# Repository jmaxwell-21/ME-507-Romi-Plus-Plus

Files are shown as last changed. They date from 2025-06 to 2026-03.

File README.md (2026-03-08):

# ME 507 Romi++ Project

Design repository for Romi++, a self-balancing differential drive robot developed for Cal Poly's ME 507 Mechanical Control Systems Design class.

## Documentation

[View the complete Doxygen code documentation](https://jmaxwell-21.github.io/ME-507-Romi-Plus-Plus/)

## GitHub File Structure

- `Firmware/` - STM32CubeIDE project source code and FSM diagrams
- `Hardware/` - Mechanical and electrical design files and information
- `Media/` -  Project photos and videos
- `docs/` - Doxygen-generated HTML documentation

---

Made by Jack Maxwell  
Cal Poly | Spring 2025

# Overview

Romi++ is a two-wheeled differential drive robot with a cylindrical body. It can be remotely controlled by either a computer or the custom [Smart Knob Controller](https://github.com/Larson-Nick/SmartKnobController) built by my partner and can drive at speeds up to 1&nbsp;m/s while autonomously maintaining balance through PID control.

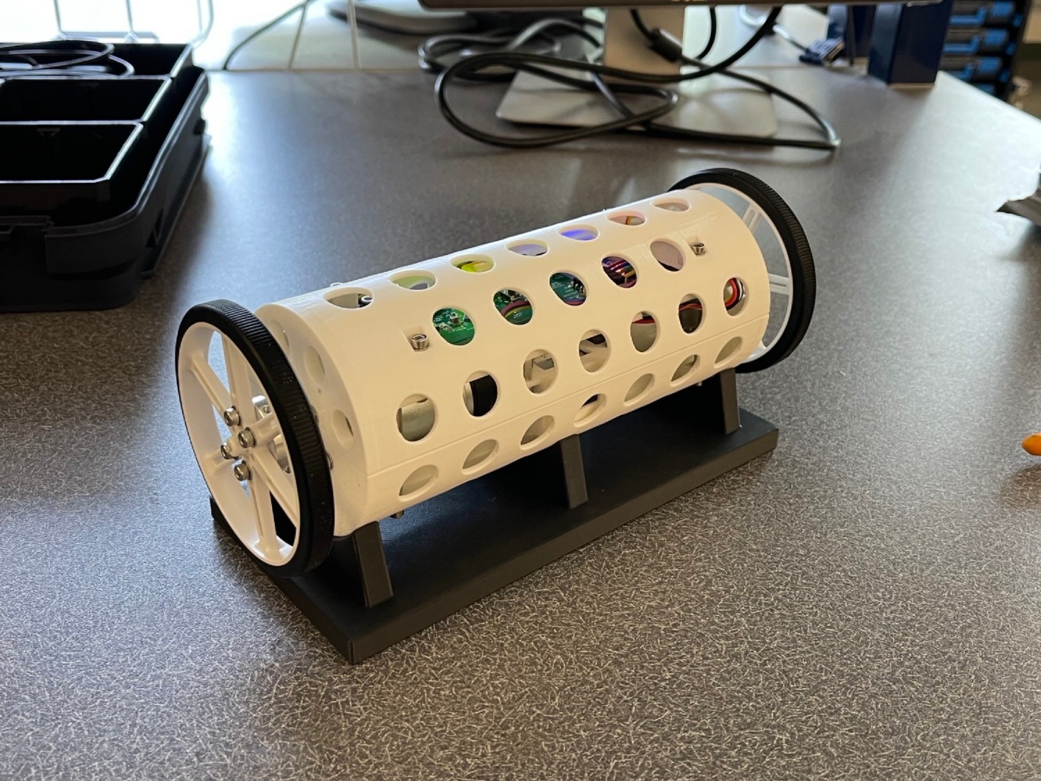
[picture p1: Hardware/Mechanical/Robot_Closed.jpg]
Robot photo


## See Romi++ in action!
<table>
  <tr>
    <td align="center" valign="top">
      <a href="https://youtube.com/shorts/c_1nM_AD648">
        <br>
        <strong>Official Project Demo</strong>
      </a>
      <p>Official project demo showcasing wireless two-wheeled robot with custom controller (using attachments before balance control was implemented).</p>
    </td>
    <td align="center" valign="top">
      <a href="https://youtube.com/shorts/LBDbpKdLq8A">
        <br>
        <strong>Bonus Project Demo</strong>
      </a>
      <p>Final demo with balance control enabled, allowing the robot to stay level while driving without attachments.</p>
    </td>
  </tr>
</table>

This project serves as a successor to my [Romi Line-Following Robot](https://github.com/finite-colin-machine/ME-405-Romi) project from ME 405 at Cal Poly. Unlike the original Romi, which used caster wheels for stability, Romi++ is cylindrical and free to rotate about its drive axis, requiring active balance control to remain upright.

Romi++ was my term project for the ME 507 Mechanical Control Systems Design class at Cal Poly. It was a perfect blend of the four core areas of mechatronics: mechanical design, electronics, embedded systems, and control systems. These aspects of my project are explained in more depth below.

## Mechanical Design

Mechanical Design

The main components of the robot are the 3D-printed cylindrical body, two motors with wheels, a battery compartment, and various fasteners. The motors are mounted beneath the mounting plate and screw into the cylinder sides. The battery sits in a small box beneath the mounting plate, while the electronics rest on top. Long standoffs connect both cylinder halves to the mounting plate.

All 3D-printed components were custom designed, while purchased components (motors, wheels, battery, fasteners) were integrated into the assembly. The challenge was ensuring proper fitment and mounting points for each component. I imported vendor-supplied CAD models into SolidWorks and iteratively refined the design to accommodate all components with appropriate mounting holes and clearances.

See the [Mechanical Design](Hardware/Mechanical) folder for more information on specific components.

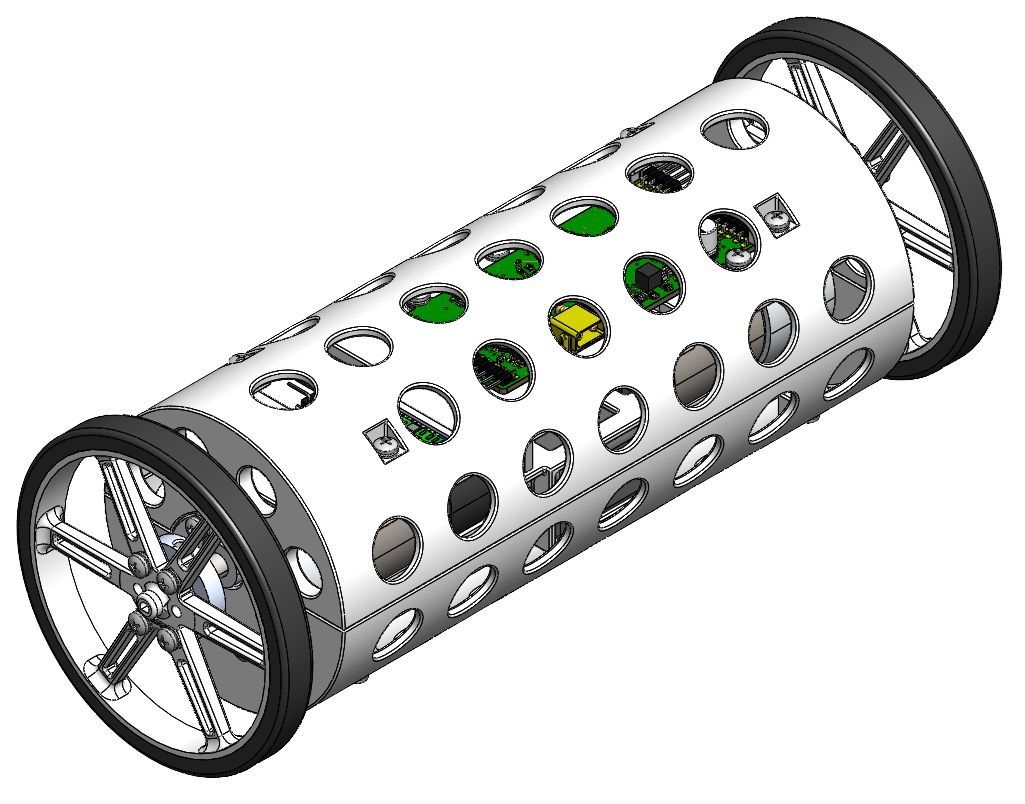
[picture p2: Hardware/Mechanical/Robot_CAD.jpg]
Robot CAD


## Electrical Design

PCB

The PCB that I designed for Romi++ was my first experience with electronics design. It took up a significant portion of the 10-week course, but it was worth it for all of the experience I gained (and the fun I had)!

The PCB has 9 main components: the power distribution system to supply various voltage levels to the system, the STM32 microcontroller to control all the components, an IMU to measure heading and pitch, 2 drivers and pin headers for the motors, a pin header for the HC-05 Bluetooth module, a pin header for the ST-Link debugger, a reset button, and a general-purpose user button. I designed the [schematic](Hardware/Electrical/PCB%20Schematic.pdf) and board layout in Fusion 360 and had it manufactured by JLCPCB.

See the [Electrical Design](Hardware/Electrical) folder for complete schematics, board layouts, and manufacturing files.

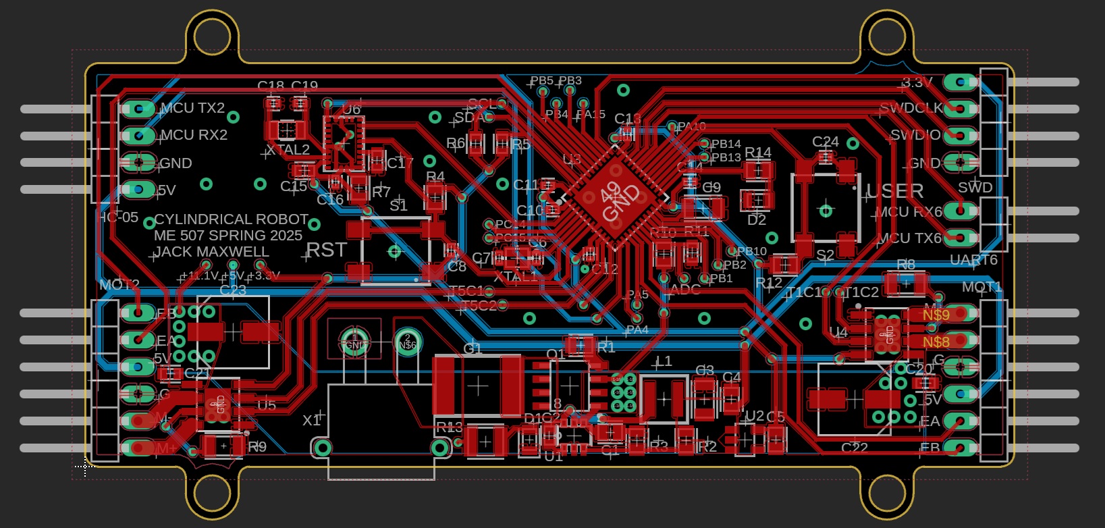
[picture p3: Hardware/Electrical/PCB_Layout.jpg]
Board Layout


### Power Distribution

The robot is powered by a 3S LiPo battery with a nominal voltage of 11.1&nbsp;V. A [fuse](https://www.digikey.com/en/products/detail/littelfuse-inc/2920l400-15mr/6234817) and a [p-channel MOSFET](https://www.digikey.com/en/products/detail/infineon-technologies/IRF7416TRPBF/856470) are used for circuit protection, and the 11.1&nbsp;V from the battery goes to the two [motor driver](https://www.digikey.com/en/products/detail/texas-instruments/DRV8231DDAR/16184249) integrated circuits. A [buck regulator](https://www.digikey.com/en/products/detail/texas-instruments/lmr54406fdbvr/15926505) is used to drop the 11.1&nbsp;V to 5&nbsp;V and provide a smooth output for the encoders and the [HC-05](https://www.electronicwings.com/sensors-modules/bluetooth-module-hc-05-), and an [LDO regulator](https://www.digikey.com/en/products/detail/texas-instruments/TPS7A2033PDBVR/13566866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) is used to drop the 5&nbsp;V to 3.3&nbsp;V to power the remaining integrated circuits.

### Microcontroller (MCU)

To run my code and control each peripheral, an [STM32F411CEU6 Microcontroller](https://www.digikey.com/en/products/detail/stmicroelectronics/STM32F411CEU6/4935720) is used. This 32-bit ARM Cortex-M4 MCU running at 100&nbsp;MHz provides sufficient processing power for real-time control loops while offering the necessary peripherals: I2C for the IMU, UART for Bluetooth communication, PWM timers for motor control, and encoder inputs for wheel speed measurement.

### Inertial Measurement Unit (IMU)

To provide heading (yaw) and pitch measurements for the robot's control system, the [BNO055](https://www.digikey.com/en/products/detail/bosch-sensortec/BNO055/6136301) 9-axis absolute orientation sensor is used. The heading data enables precise turning control, while the pitch angle is used by the balance controller to keep the robot upright. Communication with the microcontroller occurs over I2C, with the sensor providing orientation data at up to 100&nbsp;Hz for responsive control.

## Firmware and Controls

The firmware for Romi++ was developed in C/C++ using STM32CubeIDE. While driver implementations can be found in the [Firmware](Firmware) folder, this section focuses on the cooperative multitasking structure and Finite State Machine (FSM) control algorithms that enable the robot's movement.

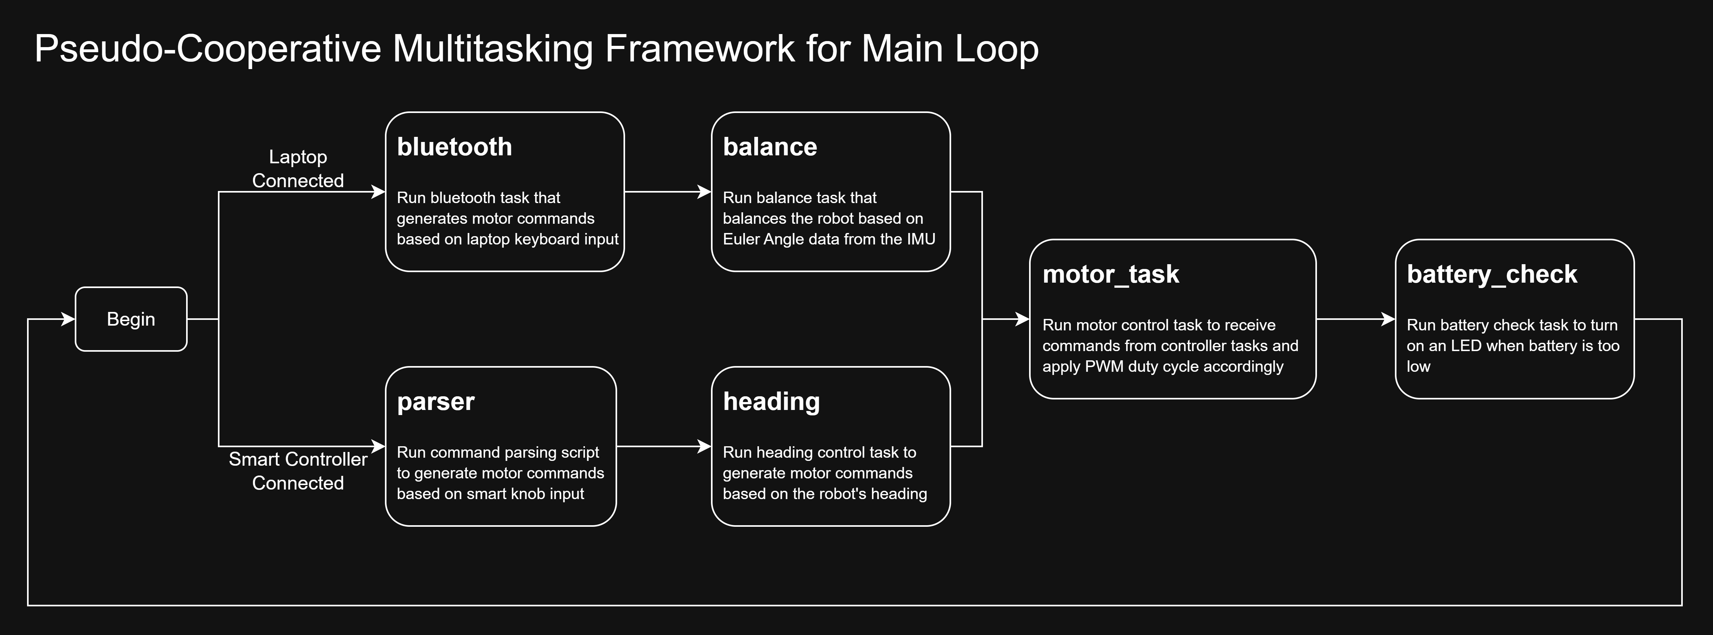
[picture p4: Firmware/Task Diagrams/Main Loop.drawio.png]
Main Loop


The firmware uses a pseudo-cooperative multitasking framework where tasks execute sequentially in the main loop. Based on the connected controller (laptop or Smart Knob), different control tasks run in order, each completing its work before passing control to the next task.

### Bluetooth Task

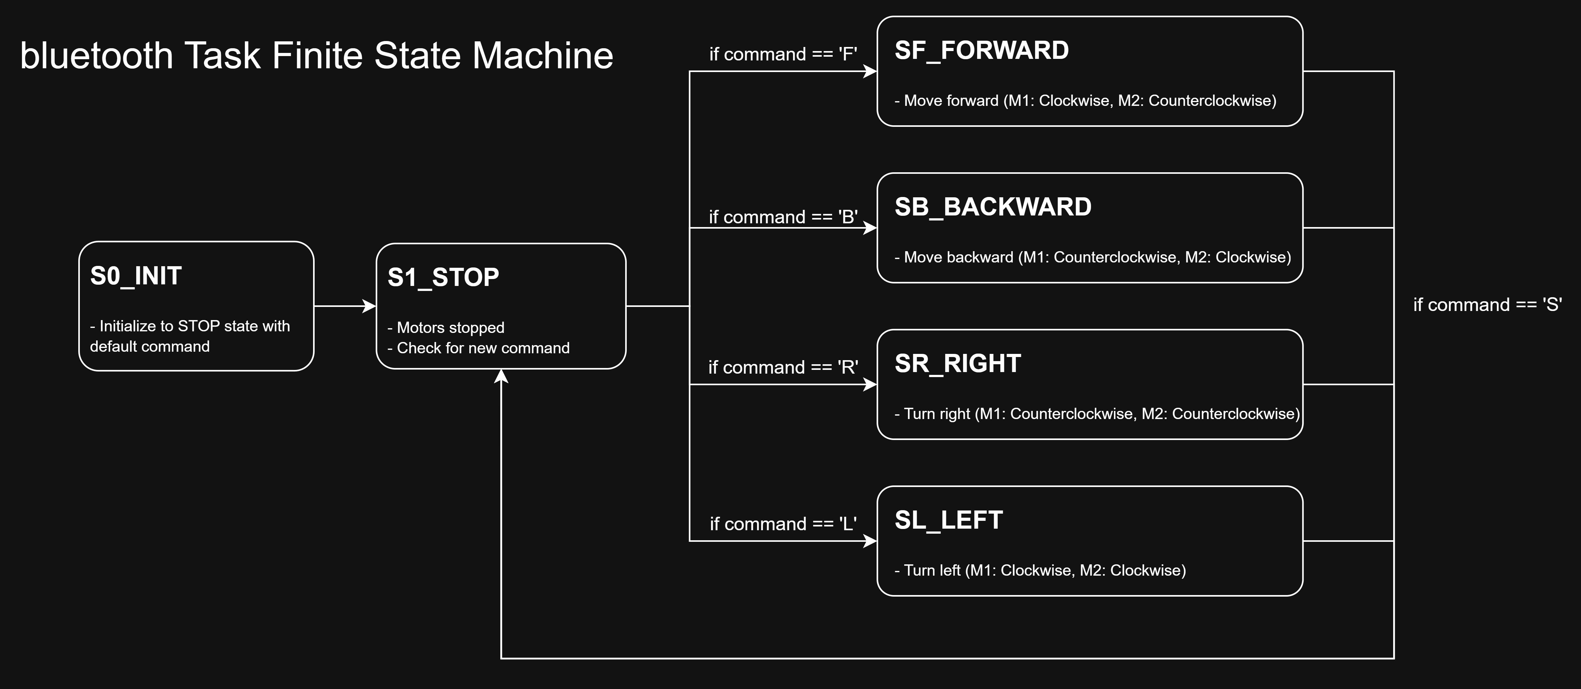
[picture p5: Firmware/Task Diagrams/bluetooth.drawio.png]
bluetooth


When a laptop is connected, the Bluetooth task runs and decodes signals sent by the [robot controller](Firmware/Additional%20Code/Robot%20Controller.py) Python script. Based on which key is pressed, the task transitions between states that command the motors to move forward, backward, left, or right. When no keys are pressed, it returns to the STOP state. This control interface was primarily used for solo testing, while the custom controller served as the main input method.

### Balance Task

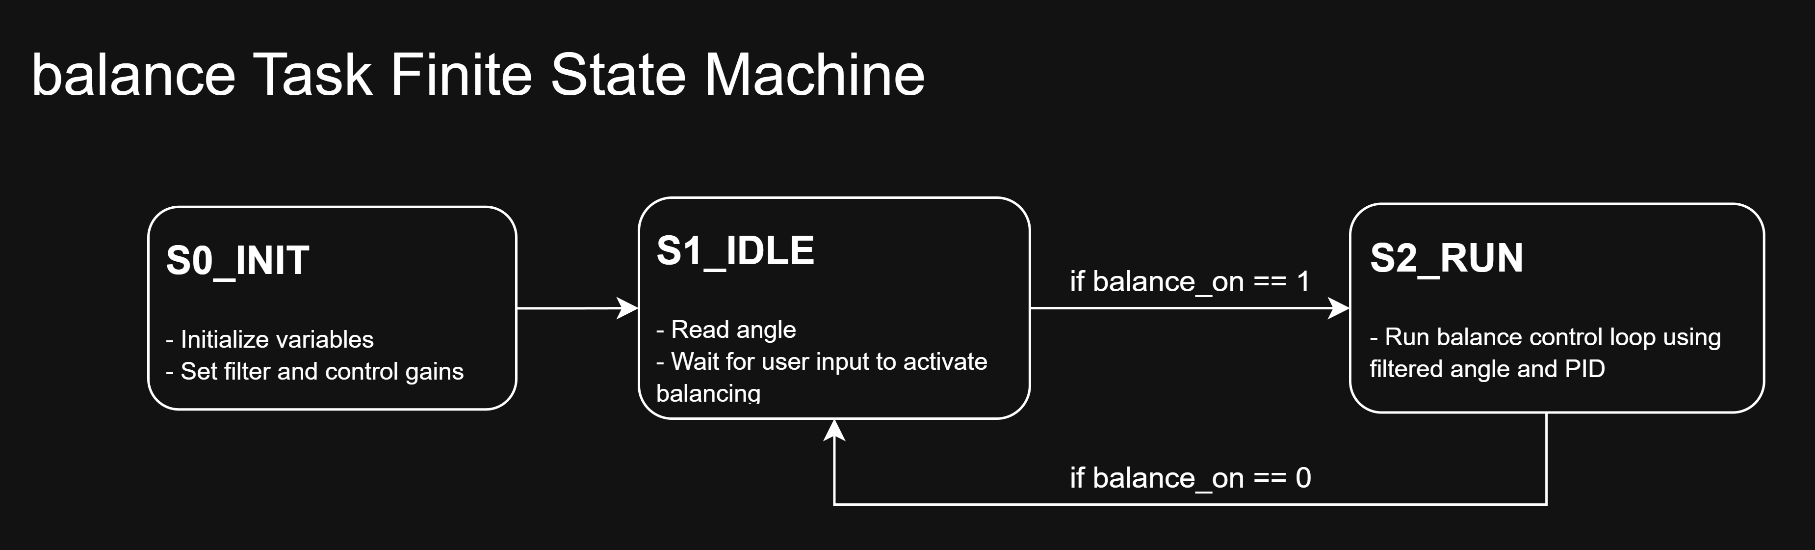
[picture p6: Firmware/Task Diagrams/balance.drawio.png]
balance


When a laptop is connected, the Balance task reads the pitch angle from the IMU and applies balance control to keep the robot upright. Because the robot is free to rotate about its drive axis, the cylindrical body tilts when the motors spin in the same direction. Without active balance control, the robot cannot drive effectively.

A PID controller compares the current pitch angle to the setpoint (0 degrees) and outputs a corrective motor effort that gets sent to the motor task. This creates a feedback loop that continuously adjusts the motors to maintain balance while driving.

The balance control toggles between IDLE and RUN states when the user button on the PCB is pressed. This allows demonstration of the robot's behavior with and without balance control enabled.

Balance control was not implemented in time for the official project demonstration, which is why an attachment was used to prevent the robot from spinning in that demo. This is also why balance control only runs while a laptop is connected and not with the Smart Knob Controller.

### Parser Task

The Parser task decodes command strings received from the Smart Knob Controller via UART IDLE-line detection with DMA reception. Commands begin with a mode character ('A', 'B', 'C', or 'D') followed by hexadecimal values for motor duty cycles or heading setpoints. The parser extracts these values and makes them available to the motor and heading control tasks.

**Supported modes:**
- **Mode A/B**: Direct motor control (M1 and M2 duty cycles)
- **Mode C**: Reserved for future use
- **Mode D**: Combined heading and motor effort control

### Heading Task

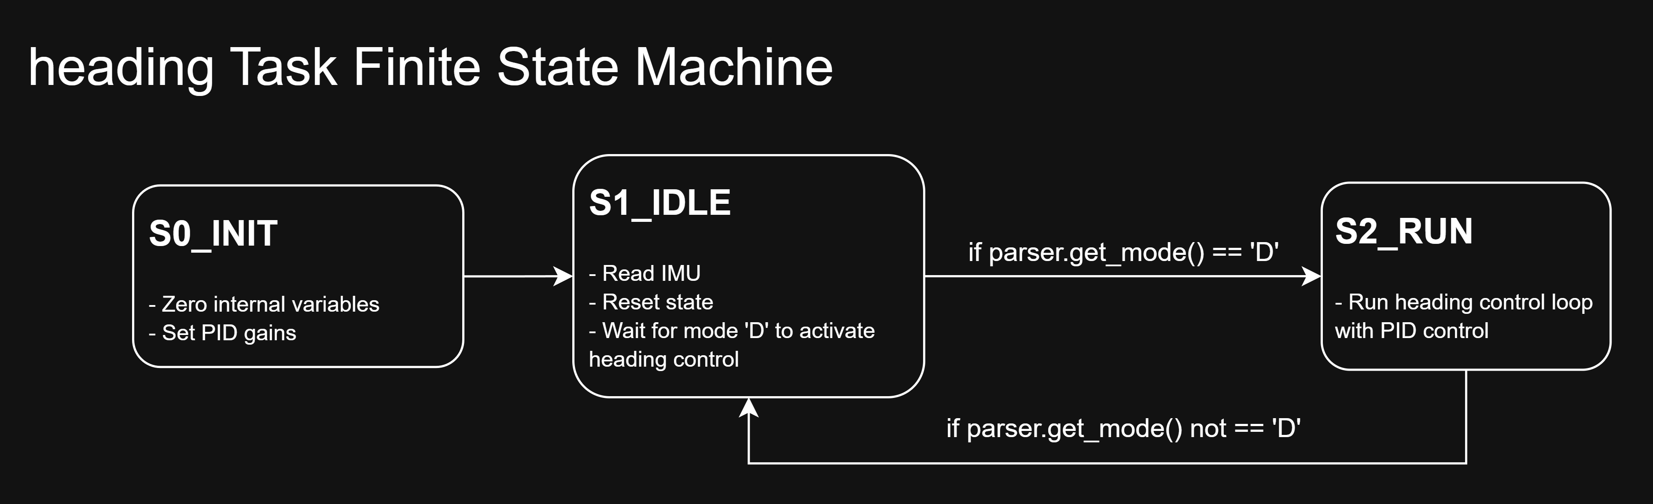
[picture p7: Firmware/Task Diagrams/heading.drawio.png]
heading


When Mode D is active (combined heading and motor control from the Smart Knob Controller), the Heading task reads the yaw angle from the IMU and controls the robot's orientation. The task tracks the robot's angular position by accumulating angle changes while handling 360-degree wraparound, creating a continuous heading reference.

A PID controller compares the current heading to the commanded setpoint and generates opposing motor efforts for differential steering. These efforts are added to any forward/backward motion commands, allowing the robot to drive while maintaining orientation.

The heading control activates only in Mode D and returns to IDLE when the controller switches modes. Pressing the user button calibrates the heading by resetting the accumulated position to match the current setpoint, which is useful for correcting drift or realigning the reference frame during operation.

### Motor Task

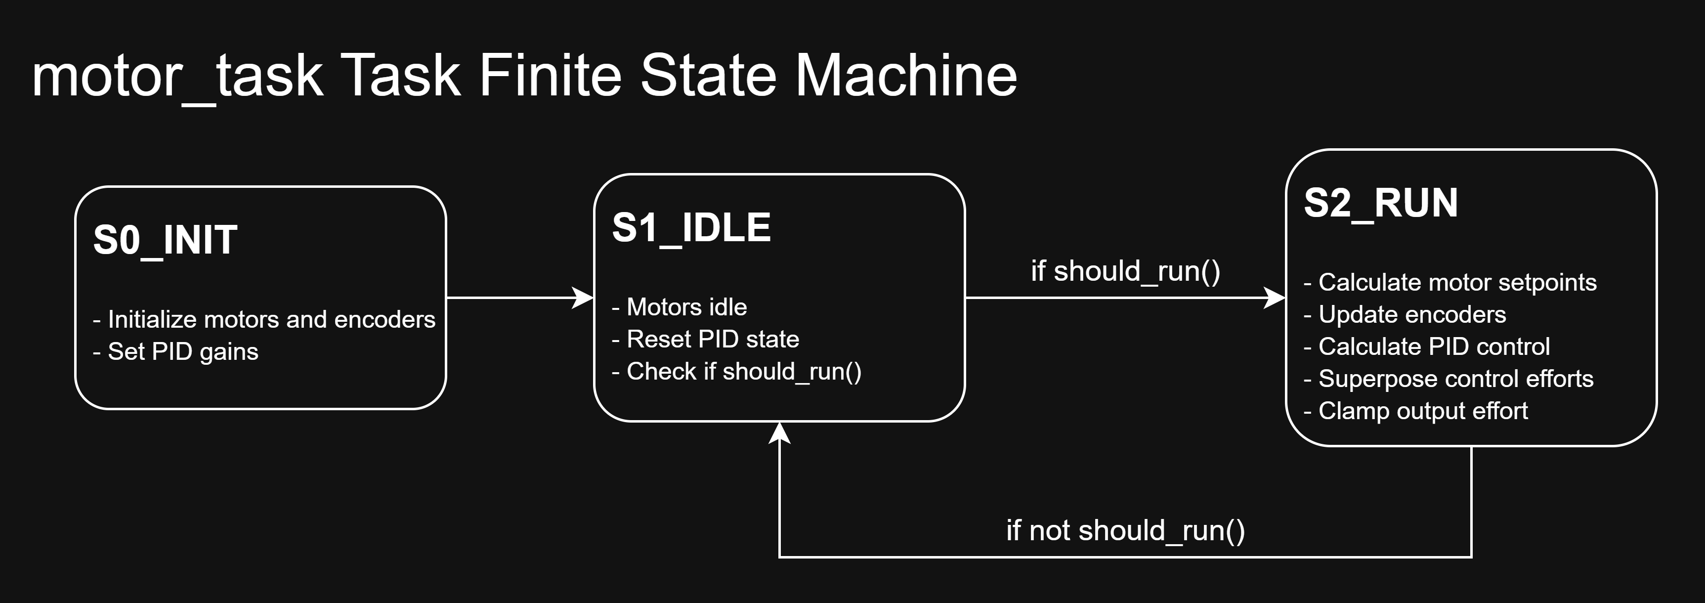
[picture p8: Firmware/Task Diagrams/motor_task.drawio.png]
motor_task


The Motor task serves as the central control hub that integrates commands from all other tasks and translates them into PWM signals for the motor drivers. It receives speed setpoints from either the Bluetooth or Parser tasks and uses encoder feedback to implement closed-loop speed control with PID.

The task continuously reads encoder speeds and calculates PID corrections to match the commanded wheel velocities. Crucially, it then superposes control efforts from the Heading and Balance tasks onto these base speed commands. This allows the robot to simultaneously drive at a target speed, maintain orientation, and stay upright.

The motor task transitions from IDLE to RUN whenever any input source provides non-zero commands or control efforts. Final motor efforts are clamped to safe PWM limits before being sent to the motor drivers, ensuring the robot operates within hardware constraints. This architecture makes the Motor task the final stage in a layered control system where multiple independent controllers work together to achieve complex behavior.

### Battery Check Task

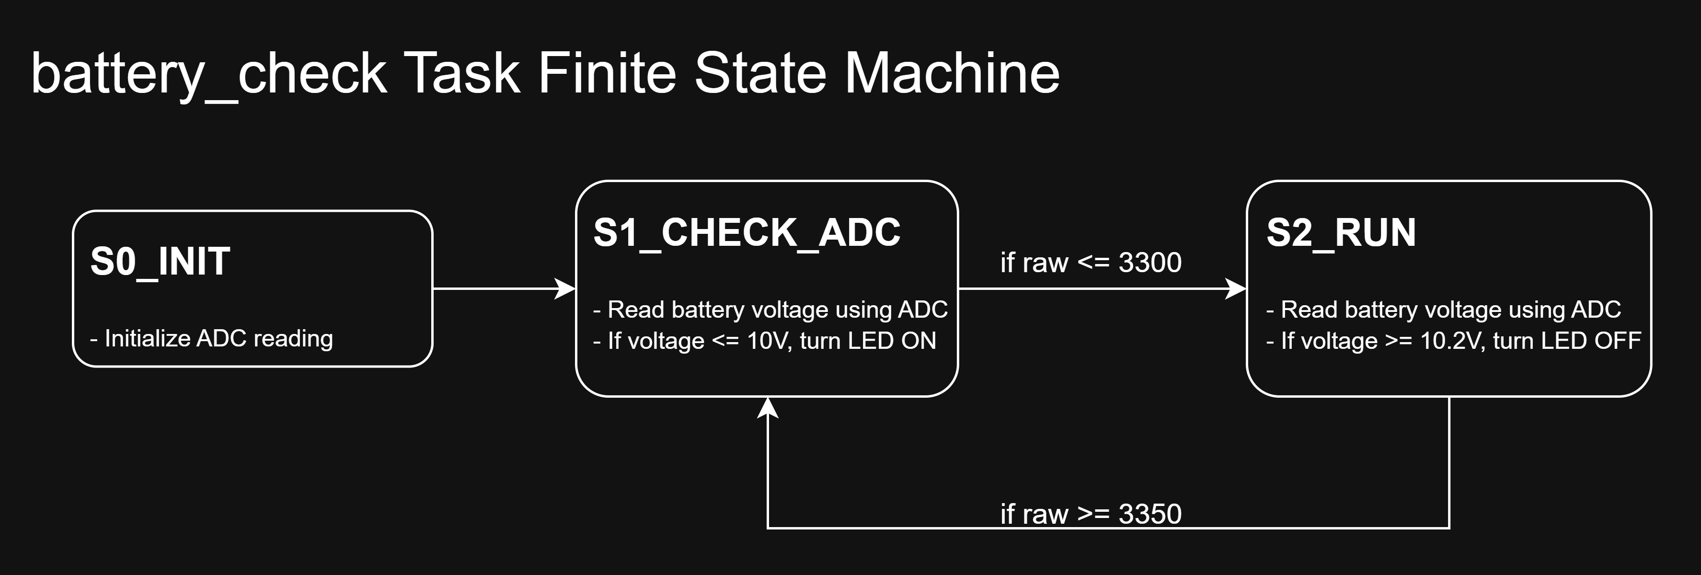
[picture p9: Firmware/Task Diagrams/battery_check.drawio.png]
battery_check


The Battery Check task monitors the battery voltage through an ADC input and provides a visual warning when power drops too low. It continuously reads the analog voltage level and compares it against threshold values to protect the LiPo battery from over-discharge.

When the battery voltage drops below approximately 10.05 V (ADC value < 3300), the task activates an LED indicator and transitions to the BATTERY_LOW state. Once in this state, the LED remains on until the voltage recovers to at least 10.20 V (ADC value > 3350), at which point it turns off and returns to normal monitoring.

This design prevents the LED from flickering on and off when the battery voltage hovers near the threshold, as motor loads can cause temporary voltage dips that recover quickly. When the battery is depleted and requires charging, it must be disconnected to do so. The specific voltage thresholds are chosen to provide a safe margin above the 3 V per cell over-discharge limit (9 V total for a 3S battery).

## Project Results and Reflection

Romi++ successfully demonstrates the integration of mechanical design, electronics, embedded systems, and control systems into a fully functional balancing robot. The final system achieves autonomous balance control, precise heading tracking, and wireless operation through two independent control interfaces.

**Key achievements:**
- DFMA-driven design with standardized fasteners and single-tool access
- Custom PCB design and fabrication with successful implementation
- Multi-layered control architecture with superposed PID controllers
- Wireless control via Bluetooth for laptop and custom controller interfaces

**Challenges and lessons learned:**

Designing the PCB was a grueling task, especially with no prior experience. Over about 4 weeks, I learned about decoupling capacitors, ground planes, trace routing, and many more topics while iterating and improving my design. The end result was a board with no defects that worked perfectly on the first try, which is something I am very proud of!

With only 3 weeks to write and test the code after receiving the PCB, the project required careful prioritization of features. Before implementing balance control, I first had to ensure my robot could communicate with the Smart Knob Controller and interpret its commands for the project demo. Tuning multiple PID controllers required systematic testing documented in the [project videos](Media).

**Future improvements:**
- Enable Bluetooth connection with Xbox/PlayStation controller for more versatile and intuitive control
- Optimize PID gains for faster response and better disturbance rejection
- Create a new iteration with omnidirectional movement, jumping capabilities, and a built-in camera, similar to the [drones in Rainbow Six Siege](https://rainbowsix.fandom.com/wiki/Drone)

This project provided hands-on experience across the full mechatronics design cycle, from initial CAD modeling through PCB design to firmware development and control system tuning. Special thanks to [Nick Larson](https://github.com/Larson-Nick) for developing the Smart Knob Controller that elevated this project's user experience.

## Media Gallery
Check out the [Media folder](Media) for photos and videos of project development. Watch the [full video playlist](https://www.youtube.com/playlist?list=PLDFOiaVsUKKqYprYMNDaC-OZPWteVwOPU) to see the robot's development from first tests to final demonstration.

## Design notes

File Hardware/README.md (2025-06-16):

# Hardware

This folder contains all electrical and mechanical design files for the Romi++ Differential Drive Robot, including PCB schematics, board layout, manufacturing assets, and CAD models.

## Contents

### `Electrical/` – Fusion PCB design files, manufacturing exports, and board reference images

- `JLCPCB Order Info/` – Gerber files, bill of materials (BOM), and pick-and-place data for PCB fabrication, see notes for more info
- `PCB Design Files/` – Schematic (`.sch`), board layout (`.brd`), 3D model (`.step`), and full Fusion 360 project archive (`.f3z`)
- Additional Files – Reference images of the board, schematic and layout PDFs

### `Mechanical/` – SolidWorks CAD files, 3D-printable models, and robot images

- `SolidWorks 2024 Part Files/` – Native `.SLDPRT` and `.SLDASM` files, including McMaster-Carr fasteners and vendor-supplied STEP models
- `STL 3-D Print Files/` – Exported `.stl` files ready for 3D printing
- `Robot BOM.csv` - Bill of materials for the mechanical assembly, see notes for more info
- Additional Files – Images of the assembled robot and CAD assembly

---

## How to Open the Files

### SolidWorks Files

1. Launch **SolidWorks 2024** or compatible version
2. Open `.SLDASM` files from `SolidWorks 2024 Part Files/`
3. Make sure subfolders (e.g., fasteners, STEP parts) are in the same root for proper assembly resolution

### Fusion 360 Files

1. Open Fusion 360
2. Go to **File → Open**
3. Select `ME 507 Romi++.f3z` to import the PCB project including schematic and layout

---

## Notes

- Mechanical Notes
    - Components not included in BOM were provided by my instructor
    - 20  8mm M3 Screws
    - 12 10mm M3 Screws
    - 12 12mm M3 Screws
    - 44 M3 Washers (.5mm thick)
    -  8 M3 Hex Nuts
- Electrical notes
    - For the JLCPCB order, some PCB components needed to be adjusted. This consisted of rotating some parts into the correct orientation seen on my board layout. For any recreations of this project, it is highly recommended to have the manufacturer review the design for you before assembly begins.

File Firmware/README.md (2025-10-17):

# Firmware

This folder contains the full STM32CubeIDE project for the STM32F411 microcontroller used in the Romi++ Differential Drive Robot.

## Contents

- `Core/` – Source code and header files for all robot software
- `Drivers/` – HAL drivers for peripherals
- `.ioc` file – STM32CubeMX configuration file
- `.project` and `.cproject` – Eclipse project files for STM32CubeIDE

- `Additional Code/` - Python script for controlling robot and STM32CubeIDE project for HC-05 Bluetooth Module configuration
- `Task Diagrams/` - Task diagrams for each FSM shown on the main page

## How to Open the Project

To open this project in STM32CubeIDE:

### Option 1: Import via `.ioc` File

1. Open STM32CubeIDE
2. Go to **File → Open Projects from File System**
3. Click **Directory…** and select the `firmware/` folder
4. STM32CubeIDE will automatically detect and import the project
5. Click **Finish**

### Option 2: Open `.project` Directly

1. Double-click the `.project` file in the `firmware/` folder
2. STM32CubeIDE will open it as a recognized workspace project

---

## Notes

- The `.ioc` file defines all clock settings, pin mappings, and peripheral configurations
- Any changes made in `.ioc` can regenerate code in `Core/` and `Drivers/`

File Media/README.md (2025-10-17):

# Project Media

This folder contains all photos and videos of my project throughout its development.

## Demonstration Videos
<table>
  <tr>
    <td align="center" valign="top">
      <a href="https://youtube.com/shorts/c_1nM_AD648">
        <br>
        <strong>First Project Demo</strong>
      </a>
      <p>Official project demo showcasing wireless two-wheeled robot with custom controller (using attachments before balance control was implemented).</p>
    </td>
    <td align="center" valign="top">
      <a href="https://youtube.com/shorts/LBDbpKdLq8A">
        <br>
        <strong>Final Project Demo</strong>
      </a>
      <p>Final demo with balance control enabled, allowing the robot to stay level while driving without attachments.</p>
    </td>
  </tr>
</table>

## Testing Videos
<table>
  <tr>
    <td align="center" valign="top">
      <a href="https://youtube.com/shorts/n4RnW4XA5BE">
        <br>
        <strong>First System Test</strong>
      </a>
      <p>Initial PCB test verifying motor control functionality.</p>
    </td>
    <td align="center" valign="top">
      <a href="https://youtube.com/shorts/uIjkk4RzHAo">
        <br>
        <strong>Bluetooth Driving Test 1</strong>
      </a>
      <p>First wireless driving test using Bluetooth control from laptop, with attachments to prevent spinning.</p>
    </td>
    <td align="center" valign="top">
      <a href="https://youtube.com/shorts/yojhLrzBfxM">
        <br>
        <strong>Bluetooth Driving Test 2</strong>
      </a>
      <p>Second Bluetooth driving test with attachments removed, showing free spinning before balance control.</p>
    </td>
    <td align="center" valign="top">
      <a href="https://youtube.com/shorts/kFbRjYCwOs8">
        <br>
        <strong>IMU Display Test</strong>
      </a>
      <p>First IMU test demonstrating real-time heading angle updates.</p>
    </td>
  </tr>
  <tr>
    <td align="center" valign="top">
      <a href="https://youtube.com/shorts/kPtjlTdcE0k">
        <br>
        <strong>Heading Control Test 1</strong>
      </a>
      <p>Initial heading control test with unstable behavior due to poor PID tuning.</p>
    </td>
    <td align="center" valign="top">
      <a href="https://youtube.com/shorts/aGWxtnayLmA">
        <br>
        <strong>Heading Control Test 2</strong>
      </a>
      <p>Improved heading controller that worked at 0 degrees but lacked robustness.</p>
    </td>
    <td align="center" valign="top">
      <a href="https://youtube.com/shorts/tQbPDnsnWS4">
        <br>
        <strong>Heading Control Test 3</strong>
      </a>
      <p>Final heading controller demonstrating quick, accurate response with minimal overshoot.</p>
    </td>
    <td align="center" valign="top">
      <a href="https://youtube.com/shorts/Og49P6c5zbM">
        <br>
        <strong>Controller Integration Test</strong>
      </a>
      <p>First test connecting to lab partner's custom controller for remote operation.</p>
    </td>
  </tr>
  <tr>
    <td align="center" valign="top">
      <a href="https://youtube.com/shorts/0uNJvMxnFvQ">
        <br>
        <strong>Speed Test</strong>
      </a>
      <p>Forward and backward motion test with custom controller at 50% speed.</p>
    </td>
    <td align="center" valign="top">
      <a href="https://youtube.com/shorts/kXgYKft2zP0">
        <br>
        <strong>Balance Control Test 1</strong>
      </a>
      <p>First balance control test using PID on pitch angle with no speed limiter.</p>
    </td>
    <td align="center" valign="top">
      <a href="https://youtube.com/shorts/U_N1_kcBDy4">
        <br>
        <strong>Balance Control Test 2</strong>
      </a>
      <p>Second balance control test with 50% speed limit for easier handling.</p>
    </td>
  </tr>
</table>

## Full Playlist
Watch all project videos here: [Project Playlist](https://www.youtube.com/playlist?list=PLDFOiaVsUKKqYprYMNDaC-OZPWteVwOPU)

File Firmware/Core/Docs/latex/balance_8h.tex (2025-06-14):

\doxysection{Inc/balance.h File Reference}
\hypertarget{balance_8h}{}\label{balance_8h}\index{Inc/balance.h@{Inc/balance.h}}

Declaration of the \doxylink{class_b_a_l_a_n_c_e}{BALANCE} class for managing robot balance using a FSM.  

{\ttfamily \#include "{}BNO055\+\_\+\+STM32.\+h"{}}\newline
{\ttfamily \#include "{}time\+\_\+utils.\+h"{}}\newline
{\ttfamily \#include $<$stdint.\+h$>$}\newline
{\ttfamily \#include $<$algorithm$>$}\newline
\doxysubsubsection*{Classes}
\begin{DoxyCompactItemize}
\item 
class \mbox{\hyperlink{class_b_a_l_a_n_c_e}{BALANCE}}
\begin{DoxyCompactList}\small\item\em Finite State Machine class for robot balance control. \end{DoxyCompactList}\end{DoxyCompactItemize}
\doxysubsubsection*{Variables}
\begin{DoxyCompactItemize}
\item 
\Hypertarget{balance_8h_a7871395ef24115844178e306695a6b39}\label{balance_8h_a7871395ef24115844178e306695a6b39} 
\mbox{\hyperlink{struct_b_n_o055___sensors__t}{BNO055\+\_\+\+Sensors\+\_\+t}} {\bfseries BNO055}
\begin{DoxyCompactList}\small\item\em External reference to BNO055 sensor data structure. \end{DoxyCompactList}\item 
\Hypertarget{balance_8h_a59cc8776b62c3d309d2ceafcfbfa504c}\label{balance_8h_a59cc8776b62c3d309d2ceafcfbfa504c} 
volatile bool {\bfseries USER}
\begin{DoxyCompactList}\small\item\em External flag indicating user button press. \end{DoxyCompactList}\end{DoxyCompactItemize}

\doxysubsection{Detailed Description}
Declaration of the \doxylink{class_b_a_l_a_n_c_e}{BALANCE} class for managing robot balance using a FSM. 

This header defines a finite state machine (FSM) class for maintaining balance of a differential drive robot using BNO055 IMU data. It includes PID control logic and internal state tracking.

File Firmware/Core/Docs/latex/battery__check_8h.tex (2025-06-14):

\doxysection{Inc/battery\+\_\+check.h File Reference}
\hypertarget{battery__check_8h}{}\label{battery__check_8h}\index{Inc/battery\_check.h@{Inc/battery\_check.h}}

Header for the \doxylink{class_b_a_t_t_e_r_y___c_h_e_c_k}{BATTERY\+\_\+\+CHECK} class that monitors battery voltage of a 3S Li\+Po battery using the ADC.  

{\ttfamily \#include $<$stm32f4xx\+\_\+hal.\+h$>$}\newline
{\ttfamily \#include $<$stdint.\+h$>$}\newline
\doxysubsubsection*{Classes}
\begin{DoxyCompactItemize}
\item 
class \mbox{\hyperlink{class_b_a_t_t_e_r_y___c_h_e_c_k}{BATTERY\+\_\+\+CHECK}}
\begin{DoxyCompactList}\small\item\em A finite state machine for monitoring battery voltage. \end{DoxyCompactList}\end{DoxyCompactItemize}
\doxysubsubsection*{Variables}
\begin{DoxyCompactItemize}
\item 
\Hypertarget{battery__check_8h_a22b804736f5648d52f639b2647d4ed13}\label{battery__check_8h_a22b804736f5648d52f639b2647d4ed13} 
ADC\+\_\+\+Handle\+Type\+Def {\bfseries hadc1}
\begin{DoxyCompactList}\small\item\em External reference to the ADC handle used for battery sensing. \end{DoxyCompactList}\end{DoxyCompactItemize}

\doxysubsection{Detailed Description}
Header for the \doxylink{class_b_a_t_t_e_r_y___c_h_e_c_k}{BATTERY\+\_\+\+CHECK} class that monitors battery voltage of a 3S Li\+Po battery using the ADC. 

Defines a finite state machine that checks battery level and signals a low voltage condition using GPIO indicators.

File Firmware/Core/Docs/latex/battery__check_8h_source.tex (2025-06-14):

\doxysection{battery\+\_\+check.\+h}
\hypertarget{battery__check_8h_source}{}\label{battery__check_8h_source}\index{Inc/battery\_check.h@{Inc/battery\_check.h}}
\mbox{\hyperlink{battery__check_8h}{Go to the documentation of this file.}}
\begin{DoxyCode}{0}
\DoxyCodeLine{00001\ \textcolor{comment}{/*}}
\DoxyCodeLine{00002\ \textcolor{comment}{\ *\ battery\_check.h}}
\DoxyCodeLine{00003\ \textcolor{comment}{\ *}}
\DoxyCodeLine{00004\ \textcolor{comment}{\ *\ \ Created\ on:\ Jun\ 4,\ 2025}}
\DoxyCodeLine{00005\ \textcolor{comment}{\ *\ \ \ \ \ \ Author:\ jacka}}
\DoxyCodeLine{00006\ \textcolor{comment}{\ */}}
\DoxyCodeLine{00007\ }
\DoxyCodeLine{00008\ \textcolor{preprocessor}{\#ifndef\ INC\_BATTERY\_CHECK\_H\_}}
\DoxyCodeLine{00009\ \textcolor{preprocessor}{\#define\ INC\_BATTERY\_CHECK\_H\_}}
\DoxyCodeLine{00010\ }
\DoxyCodeLine{00017\ }
\DoxyCodeLine{00018\ \textcolor{preprocessor}{\#include\ <stm32f4xx\_hal.h>}}
\DoxyCodeLine{00019\ \textcolor{preprocessor}{\#include\ <stdint.h>}}
\DoxyCodeLine{00020\ }
\DoxyCodeLine{00022\ \textcolor{keyword}{extern}\ ADC\_HandleTypeDef\ \mbox{\hyperlink{battery__check_8h_a22b804736f5648d52f639b2647d4ed13}{hadc1}};}
\DoxyCodeLine{00023\ }
\DoxyCodeLine{00030\ \textcolor{keyword}{class\ }\mbox{\hyperlink{class_b_a_t_t_e_r_y___c_h_e_c_k_aed5ac8125ffc7805a9cf07b1544a488d}{BATTERY\_CHECK}}}
\DoxyCodeLine{00031\ \{}
\DoxyCodeLine{00032\ \textcolor{keyword}{public}:}
\DoxyCodeLine{00037\ \ \ \ \ \textcolor{keyword}{typedef}\ \textcolor{keyword}{enum}\ \mbox{\hyperlink{class_b_a_t_t_e_r_y___c_h_e_c_k_ae999e6f209b67a67364d82a2820553a2}{state}}}
\DoxyCodeLine{00038\ \ \ \ \ \{}
\DoxyCodeLine{00039\ \ \ \ \ \ \ \ \ \mbox{\hyperlink{class_b_a_t_t_e_r_y___c_h_e_c_k_ae999e6f209b67a67364d82a2820553a2a2efb3206dce96a77ef043a7b0598337f}{S0\_INIT}},\ \ \ \ \ \ \ \ \ }
\DoxyCodeLine{00040\ \ \ \ \ \ \ \ \ \mbox{\hyperlink{class_b_a_t_t_e_r_y___c_h_e_c_k_ae999e6f209b67a67364d82a2820553a2ab7b987c14e4c84315b0df446d7552718}{S1\_CHECK\_ADC}},\ \ \ \ }
\DoxyCodeLine{00041\ \ \ \ \ \ \ \ \ \mbox{\hyperlink{class_b_a_t_t_e_r_y___c_h_e_c_k_ae999e6f209b67a67364d82a2820553a2a6fd5d034e05dfe1a3f98d474c8f8a6fc}{S2\_BATTERY\_LOW}}\ \ \ }
\DoxyCodeLine{00042\ \ \ \ \ \}\ state\_t;}
\DoxyCodeLine{00043\ }
\DoxyCodeLine{00047\ \ \ \ \ \mbox{\hyperlink{class_b_a_t_t_e_r_y___c_h_e_c_k_aed5ac8125ffc7805a9cf07b1544a488d}{BATTERY\_CHECK}}();}
\DoxyCodeLine{00048\ }
\DoxyCodeLine{00053\ \ \ \ \ \textcolor{keywordtype}{void}\ \mbox{\hyperlink{class_b_a_t_t_e_r_y___c_h_e_c_k_a39b04b12471e7aae081fd1b457e70b98}{run}}(\textcolor{keywordtype}{void});}
\DoxyCodeLine{00054\ }
\DoxyCodeLine{00055\ \textcolor{keyword}{private}:}
\DoxyCodeLine{00056\ \ \ \ \ state\_t\ \mbox{\hyperlink{class_b_a_t_t_e_r_y___c_h_e_c_k_ae999e6f209b67a67364d82a2820553a2}{state}};\ \ }
\DoxyCodeLine{00057\ \ \ \ \ uint16\_t\ raw;\ \ \ }
\DoxyCodeLine{00058\ \};}
\DoxyCodeLine{00059\ }
\DoxyCodeLine{00060\ \textcolor{preprocessor}{\#endif\ }\textcolor{comment}{/*\ INC\_BATTERY\_CHECK\_H\_\ */}\textcolor{preprocessor}{}}

\end{DoxyCode}

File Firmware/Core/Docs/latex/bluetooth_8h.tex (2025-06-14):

\doxysection{Inc/bluetooth.h File Reference}
\hypertarget{bluetooth_8h}{}\label{bluetooth_8h}\index{Inc/bluetooth.h@{Inc/bluetooth.h}}

Bluetooth command handler for robot control.  

{\ttfamily \#include $<$stdint.\+h$>$}\newline
\doxysubsubsection*{Classes}
\begin{DoxyCompactItemize}
\item 
class \mbox{\hyperlink{class_b_l_u_e_t_o_o_t_h}{BLUETOOTH}}
\begin{DoxyCompactList}\small\item\em Finite State Machine for Bluetooth-\/based control input. \end{DoxyCompactList}\end{DoxyCompactItemize}
\doxysubsubsection*{Variables}
\begin{DoxyCompactItemize}
\item 
\Hypertarget{bluetooth_8h_a63996c688e64a8523490c422fb8aa722}\label{bluetooth_8h_a63996c688e64a8523490c422fb8aa722} 
int32\+\_\+t {\bfseries V}
\begin{DoxyCompactList}\small\item\em Velocity setpoint (in encoder counts/sec) received via Bluetooth. \end{DoxyCompactList}\end{DoxyCompactItemize}

\doxysubsection{Detailed Description}
Bluetooth command handler for robot control. 

This file declares the \doxylink{class_b_l_u_e_t_o_o_t_h}{BLUETOOTH} class, which implements a finite state machine that processes commands received via a Bluetooth module (HC-\/05). It translates commands into motor setpoints for directional control.

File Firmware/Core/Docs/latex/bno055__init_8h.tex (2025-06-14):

\doxysection{Inc/bno055\+\_\+init.h File Reference}
\hypertarget{bno055__init_8h}{}\label{bno055__init_8h}\index{Inc/bno055\_init.h@{Inc/bno055\_init.h}}

BNO055 IMU initialization interface.  

{\ttfamily \#include "{}BNO055\+\_\+\+STM32.\+h"{}}\newline
{\ttfamily \#include "{}stm32f4xx\+\_\+hal.\+h"{}}\newline
{\ttfamily \#include $<$stdio.\+h$>$}\newline
{\ttfamily \#include $<$stdint.\+h$>$}\newline
\doxysubsubsection*{Functions}
\begin{DoxyCompactItemize}
\item 
void \mbox{\hyperlink{bno055__init_8h_a1d6f7a4e7397d8b2d3a47b1c743cb33d}{Sensor\+\_\+\+Init}} (void)
\begin{DoxyCompactList}\small\item\em Initializes the BNO055 IMU sensor and applies configuration. \end{DoxyCompactList}\end{DoxyCompactItemize}
\doxysubsubsection*{Variables}
\begin{DoxyCompactItemize}
\item 
uint8\+\_\+t \mbox{\hyperlink{bno055__init_8h_a56438006451da8eae4c0fb3f2eded3e7}{Offset\+Datas}} \mbox{[}22\mbox{]}
\begin{DoxyCompactList}\small\item\em Array storing sensor offset and calibration data. \end{DoxyCompactList}\end{DoxyCompactItemize}

\doxysubsection{Detailed Description}
BNO055 IMU initialization interface. 

Provides function prototype for initializing the BNO055 sensor. Also declares a buffer for storing sensor offset calibration data. 

\label{doc-func-members}
\Hypertarget{bno055__init_8h_doc-func-members}
\doxysubsection{Function Documentation}
\Hypertarget{bno055__init_8h_a1d6f7a4e7397d8b2d3a47b1c743cb33d}\index{bno055\_init.h@{bno055\_init.h}!Sensor\_Init@{Sensor\_Init}}
\index{Sensor\_Init@{Sensor\_Init}!bno055\_init.h@{bno055\_init.h}}
\doxysubsubsection{\texorpdfstring{Sensor\_Init()}{Sensor\_Init()}}
{\footnotesize\ttfamily \label{bno055__init_8h_a1d6f7a4e7397d8b2d3a47b1c743cb33d} 
void Sensor\+\_\+\+Init (\begin{DoxyParamCaption}\item[{void}]{}{}\end{DoxyParamCaption})}

Initializes the BNO055 IMU sensor and applies configuration. 

This function sets up sensor mode, units, and optional calibration offsets.

Initializes the BNO055 IMU sensor and applies configuration.

Configures the BNO055 with normal operating mode, Android orientation, and unit settings. Applies hard-\/coded offset values for faster startup. Optional re-\/calibration section is provided but commented out. \begin{DoxyNote}{Note}
This writes previously stored sensor offsets directly to the IMU, bypassing manual calibration. This is useful for consistent startup behavior.
\end{DoxyNote}

\label{doc-var-members}
\Hypertarget{bno055__init_8h_doc-var-members}
\doxysubsection{Variable Documentation}
\Hypertarget{bno055__init_8h_a56438006451da8eae4c0fb3f2eded3e7}\index{bno055\_init.h@{bno055\_init.h}!OffsetDatas@{OffsetDatas}}
\index{OffsetDatas@{OffsetDatas}!bno055\_init.h@{bno055\_init.h}}
\doxysubsubsection{\texorpdfstring{OffsetDatas}{OffsetDatas}}
{\footnotesize\ttfamily \label{bno055__init_8h_a56438006451da8eae4c0fb3f2eded3e7} 
uint8\+\_\+t Offset\+Datas\mbox{[}22\mbox{]}\hspace{0.3cm}{\ttfamily [extern]}}

Array storing sensor offset and calibration data. 

Contains 22 bytes used to apply or retrieve sensor calibration.

Array storing sensor offset and calibration data.

Pre-\/collected sensor offsets to avoid re-\/calibration on every startup. If initialization parameters change, these offsets may become invalid.

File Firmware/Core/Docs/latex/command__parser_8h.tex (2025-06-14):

\doxysection{Inc/command\+\_\+parser.h File Reference}
\hypertarget{command__parser_8h}{}\label{command__parser_8h}\index{Inc/command\_parser.h@{Inc/command\_parser.h}}

Header for UART command parsing module.  

{\ttfamily \#include "{}stm32f4xx\+\_\+hal.\+h"{}}\newline
{\ttfamily \#include $<$stdint.\+h$>$}\newline
\doxysubsubsection*{Macros}
\begin{DoxyCompactItemize}
\item 
\Hypertarget{command__parser_8h_a6b20d41d6252e9871430c242cb1a56e7}\label{command__parser_8h_a6b20d41d6252e9871430c242cb1a56e7} 
\#define {\bfseries BUFFER\+\_\+\+SIZE}~64
\begin{DoxyCompactList}\small\item\em Maximum buffer size for incoming UART command stream. \end{DoxyCompactList}\end{DoxyCompactItemize}
\doxysubsubsection*{Variables}
\begin{DoxyCompactItemize}
\item 
\Hypertarget{command__parser_8h_a7859af7e1d2d58c1bc67f781bbfbe818}\label{command__parser_8h_a7859af7e1d2d58c1bc67f781bbfbe818} 
uint8\+\_\+t {\bfseries rx\+\_\+buffer} \mbox{[}\mbox{\hyperlink{command__parser_8h_a6b20d41d6252e9871430c242cb1a56e7}{BUFFER\+\_\+\+SIZE}}\mbox{]}
\begin{DoxyCompactList}\small\item\em DMA-\/compatible receive buffer for UART. \end{DoxyCompactList}\item 
\Hypertarget{command__parser_8h_a2359bfa4a10109d5dcc2e002cb8ece47}\label{command__parser_8h_a2359bfa4a10109d5dcc2e002cb8ece47} 
uint8\+\_\+t {\bfseries buffer\+\_\+index}
\begin{DoxyCompactList}\small\item\em Current write index into rx\+\_\+buffer. \end{DoxyCompactList}\item 
\Hypertarget{command__parser_8h_a6dcf3de33714573b301e5db87df1f4f9}\label{command__parser_8h_a6dcf3de33714573b301e5db87df1f4f9} 
volatile uint8\+\_\+t {\bfseries command\+\_\+ready}
\begin{DoxyCompactList}\small\item\em Flag indicating a complete command is available. \end{DoxyCompactList}\end{DoxyCompactItemize}

\doxysubsection{Detailed Description}
Header for UART command parsing module. 

Provides a C++ class for interpreting control messages received via DMA UART from an external controller. Includes setpoint extraction for motors and heading.

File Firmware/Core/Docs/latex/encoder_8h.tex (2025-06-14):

\doxysection{Inc/encoder.h File Reference}
\hypertarget{encoder_8h}{}\label{encoder_8h}\index{Inc/encoder.h@{Inc/encoder.h}}

Quadrature encoder interface for STM32 timers.  

{\ttfamily \#include "{}time\+\_\+utils.\+h"{}}\newline
{\ttfamily \#include $<$stm32f4xx\+\_\+hal.\+h$>$}\newline
\doxysubsubsection*{Classes}
\begin{DoxyCompactItemize}
\item 
struct \mbox{\hyperlink{structencoder__t}{encoder\+\_\+t}}
\begin{DoxyCompactList}\small\item\em Structure for tracking encoder state and motion data. \end{DoxyCompactList}\end{DoxyCompactItemize}
\doxysubsubsection*{Functions}
\begin{DoxyCompactItemize}
\item 
void \mbox{\hyperlink{encoder_8h_a0d281a523aec02f31d4feb4bb3f35d51}{encoder\+\_\+init}} (\mbox{\hyperlink{structencoder__t}{encoder\+\_\+t}} \texorpdfstring{$\ast$}{*}encoder, TIM\+\_\+\+Handle\+Type\+Def \texorpdfstring{$\ast$}{*}htim)
\begin{DoxyCompactList}\small\item\em Initializes an encoder structure with a given timer. \end{DoxyCompactList}\item 
void \mbox{\hyperlink{encoder_8h_a01f4459d7b34aebb118a13ab9f8a80ae}{encoder\+\_\+update}} (\mbox{\hyperlink{structencoder__t}{encoder\+\_\+t}} \texorpdfstring{$\ast$}{*}encoder)
\begin{DoxyCompactList}\small\item\em Updates the encoder\textquotesingle{}s internal position, delta, and speed. \end{DoxyCompactList}\item 
int32\+\_\+t \mbox{\hyperlink{encoder_8h_a11e428db5d837a0db2d37f04a95e74e5}{encoder\+\_\+getposition}} (\mbox{\hyperlink{structencoder__t}{encoder\+\_\+t}} \texorpdfstring{$\ast$}{*}encoder)
\begin{DoxyCompactList}\small\item\em Returns the current position (accumulated counts) of the encoder. \end{DoxyCompactList}\item 
int32\+\_\+t \mbox{\hyperlink{encoder_8h_a35cc8efb5877f4de74fae409748be0dc}{encoder\+\_\+getdelta}} (\mbox{\hyperlink{structencoder__t}{encoder\+\_\+t}} \texorpdfstring{$\ast$}{*}encoder)
\begin{DoxyCompactList}\small\item\em Returns the most recent change in encoder count. \end{DoxyCompactList}\item 
float \mbox{\hyperlink{encoder_8h_a6b1ea1a649b4593daa55f65094db7f04}{encoder\+\_\+getspeed}} (\mbox{\hyperlink{structencoder__t}{encoder\+\_\+t}} \texorpdfstring{$\ast$}{*}encoder)
\begin{DoxyCompactList}\small\item\em Returns the current speed in counts per second. \end{DoxyCompactList}\item 
void \mbox{\hyperlink{encoder_8h_a839c6e77e921e4b73f91b67e141dd1ac}{encoder\+\_\+reset}} (\mbox{\hyperlink{structencoder__t}{encoder\+\_\+t}} \texorpdfstring{$\ast$}{*}encoder)
\begin{DoxyCompactList}\small\item\em Resets encoder position and delta tracking. \end{DoxyCompactList}\end{DoxyCompactItemize}

\doxysubsection{Detailed Description}
Quadrature encoder interface for STM32 timers. 

Provides data structures and functions for tracking position, velocity, and delta counts using hardware timers configured in encoder mode. 

\label{doc-func-members}
\Hypertarget{encoder_8h_doc-func-members}
\doxysubsection{Function Documentation}
\Hypertarget{encoder_8h_a35cc8efb5877f4de74fae409748be0dc}\index{encoder.h@{encoder.h}!encoder\_getdelta@{encoder\_getdelta}}
\index{encoder\_getdelta@{encoder\_getdelta}!encoder.h@{encoder.h}}
\doxysubsubsection{\texorpdfstring{encoder\_getdelta()}{encoder\_getdelta()}}
{\footnotesize\ttfamily \label{encoder_8h_a35cc8efb5877f4de74fae409748be0dc} 
int32\+\_\+t encoder\+\_\+getdelta (\begin{DoxyParamCaption}\item[{\mbox{\hyperlink{structencoder__t}{encoder\+\_\+t}} \texorpdfstring{$\ast$}{*}}]{encoder}{}\end{DoxyParamCaption})}

Returns the most recent change in encoder count. 

\begin{DoxyParams}{Parameters}
{\em encoder} & Pointer to encoder structure. \\
\hline
\end{DoxyParams}
\begin{DoxyReturn}{Returns}
Signed 32-\/bit count delta since last update.
\end{DoxyReturn}
Returns the most recent change in encoder count.

\begin{DoxyParams}{Parameters}
{\em encoder} & Pointer to encoder structure. \\
\hline
\end{DoxyParams}
\begin{DoxyReturn}{Returns}
Count difference since the last update. 
\end{DoxyReturn}
\Hypertarget{encoder_8h_a11e428db5d837a0db2d37f04a95e74e5}\index{encoder.h@{encoder.h}!encoder\_getposition@{encoder\_getposition}}
\index{encoder\_getposition@{encoder\_getposition}!encoder.h@{encoder.h}}
\doxysubsubsection{\texorpdfstring{encoder\_getposition()}{encoder\_getposition()}}
{\footnotesize\ttfamily \label{encoder_8h_a11e428db5d837a0db2d37f04a95e74e5} 
int32\+\_\+t encoder\+\_\+getposition (\begin{DoxyParamCaption}\item[{\mbox{\hyperlink{structencoder__t}{encoder\+\_\+t}} \texorpdfstring{$\ast$}{*}}]{encoder}{}\end{DoxyParamCaption})}

Returns the current position (accumulated counts) of the encoder. 

\begin{DoxyParams}{Parameters}
{\em encoder} & Pointer to encoder structure. \\
\hline
\end{DoxyParams}
\begin{DoxyReturn}{Returns}
Signed 32-\/bit position count.
\end{DoxyReturn}
Returns the current position (accumulated counts) of the encoder.

\begin{DoxyParams}{Parameters}
{\em encoder} & Pointer to encoder structure. \\
\hline
\end{DoxyParams}
\begin{DoxyReturn}{Returns}
Current position in encoder counts. 
\end{DoxyReturn}
\Hypertarget{encoder_8h_a6b1ea1a649b4593daa55f65094db7f04}\index{encoder.h@{encoder.h}!encoder\_getspeed@{encoder\_getspeed}}
\index{encoder\_getspeed@{encoder\_getspeed}!encoder.h@{encoder.h}}
\doxysubsubsection{\texorpdfstring{encoder\_getspeed()}{encoder\_getspeed()}}
{\footnotesize\ttfamily \label{encoder_8h_a6b1ea1a649b4593daa55f65094db7f04} 
float encoder\+\_\+getspeed (\begin{DoxyParamCaption}\item[{\mbox{\hyperlink{structencoder__t}{encoder\+\_\+t}} \texorpdfstring{$\ast$}{*}}]{encoder}{}\end{DoxyParamCaption})}

Returns the current speed in counts per second. 

\begin{DoxyParams}{Parameters}
{\em encoder} & Pointer to encoder structure. \\
\hline
\end{DoxyParams}
\begin{DoxyReturn}{Returns}
Speed in CPS (counts per second).
\end{DoxyReturn}
Returns the current speed in counts per second.

\begin{DoxyParams}{Parameters}
{\em encoder} & Pointer to encoder structure. \\
\hline
\end{DoxyParams}
\begin{DoxyReturn}{Returns}
Speed in counts per second (CPS). 
\end{DoxyReturn}
\Hypertarget{encoder_8h_a0d281a523aec02f31d4feb4bb3f35d51}\index{encoder.h@{encoder.h}!encoder\_init@{encoder\_init}}
\index{encoder\_init@{encoder\_init}!encoder.h@{encoder.h}}
\doxysubsubsection{\texorpdfstring{encoder\_init()}{encoder\_init()}}
{\footnotesize\ttfamily \label{encoder_8h_a0d281a523aec02f31d4feb4bb3f35d51} 
void encoder\+\_\+init (\begin{DoxyParamCaption}\item[{\mbox{\hyperlink{structencoder__t}{encoder\+\_\+t}} \texorpdfstring{$\ast$}{*}}]{encoder}{, }\item[{TIM\+\_\+\+Handle\+Type\+Def \texorpdfstring{$\ast$}{*}}]{htim}{}\end{DoxyParamCaption})}

Initializes an encoder structure with a given timer. 

\begin{DoxyParams}{Parameters}
{\em encoder} & Pointer to encoder structure. \\
\hline
{\em htim} & Pointer to initialized TIM\+\_\+\+Handle\+Type\+Def configured for encoder mode.\\
\hline
\end{DoxyParams}
Initializes an encoder structure with a given timer.

\begin{DoxyParams}{Parameters}
{\em encoder} & Pointer to encoder structure to initialize. \\
\hline
{\em htim} & Pointer to a TIM\+\_\+\+Handle\+Type\+Def configured in encoder mode. \\
\hline
\end{DoxyParams}
\Hypertarget{encoder_8h_a839c6e77e921e4b73f91b67e141dd1ac}\index{encoder.h@{encoder.h}!encoder\_reset@{encoder\_reset}}
\index{encoder\_reset@{encoder\_reset}!encoder.h@{encoder.h}}
\doxysubsubsection{\texorpdfstring{encoder\_reset()}{encoder\_reset()}}
{\footnotesize\ttfamily \label{encoder_8h_a839c6e77e921e4b73f91b67e141dd1ac} 
void encoder\+\_\+reset (\begin{DoxyParamCaption}\item[{\mbox{\hyperlink{structencoder__t}{encoder\+\_\+t}} \texorpdfstring{$\ast$}{*}}]{encoder}{}\end{DoxyParamCaption})}

Resets encoder position and delta tracking. 

\begin{DoxyParams}{Parameters}
{\em encoder} & Pointer to encoder structure.\\
\hline
\end{DoxyParams}
Resets encoder position and delta tracking.

\begin{DoxyParams}{Parameters}
{\em encoder} & Pointer to encoder structure. \\
\hline
\end{DoxyParams}
\Hypertarget{encoder_8h_a01f4459d7b34aebb118a13ab9f8a80ae}\index{encoder.h@{encoder.h}!encoder\_update@{encoder\_update}}
\index{encoder\_update@{encoder\_update}!encoder.h@{encoder.h}}
\doxysubsubsection{\texorpdfstring{encoder\_update()}{encoder\_update()}}
{\footnotesize\ttfamily \label{encoder_8h_a01f4459d7b34aebb118a13ab9f8a80ae} 
void encoder\+\_\+update (\begin{DoxyParamCaption}\item[{\mbox{\hyperlink{structencoder__t}{encoder\+\_\+t}} \texorpdfstring{$\ast$}{*}}]{encoder}{}\end{DoxyParamCaption})}

Updates the encoder\textquotesingle{}s internal position, delta, and speed. 

\begin{DoxyParams}{Parameters}
{\em encoder} & Pointer to encoder structure.\\
\hline
\end{DoxyParams}
Updates the encoder\textquotesingle{}s internal position, delta, and speed.

Computes the count delta between updates and handles overflow. Speed is calculated in counts per second (CPS). 
\begin{DoxyParams}{Parameters}
{\em encoder} & Pointer to encoder structure to update. \\
\hline
\end{DoxyParams}

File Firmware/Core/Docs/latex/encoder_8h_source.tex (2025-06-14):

\doxysection{encoder.\+h}
\hypertarget{encoder_8h_source}{}\label{encoder_8h_source}\index{Inc/encoder.h@{Inc/encoder.h}}
\mbox{\hyperlink{encoder_8h}{Go to the documentation of this file.}}
\begin{DoxyCode}{0}
\DoxyCodeLine{00001\ \textcolor{comment}{/*}}
\DoxyCodeLine{00002\ \textcolor{comment}{\ *\ encoder.h}}
\DoxyCodeLine{00003\ \textcolor{comment}{\ *}}
\DoxyCodeLine{00004\ \textcolor{comment}{\ *\ \ Created\ on:\ May\ 27,\ 2025}}
\DoxyCodeLine{00005\ \textcolor{comment}{\ *\ \ \ \ \ \ Author:\ jacka}}
\DoxyCodeLine{00006\ \textcolor{comment}{\ */}}
\DoxyCodeLine{00007\ }
\DoxyCodeLine{00008\ \textcolor{preprocessor}{\#ifndef\ INC\_ENCODER\_H\_}}
\DoxyCodeLine{00009\ \textcolor{preprocessor}{\#define\ INC\_ENCODER\_H\_}}
\DoxyCodeLine{00010\ }
\DoxyCodeLine{00017\ }
\DoxyCodeLine{00018\ \textcolor{preprocessor}{\#ifdef\ \_\_cplusplus}}
\DoxyCodeLine{00019\ \textcolor{keyword}{extern}\ \textcolor{stringliteral}{"{}C"{}}\ \{}
\DoxyCodeLine{00020\ \textcolor{preprocessor}{\#endif}}
\DoxyCodeLine{00021\ }
\DoxyCodeLine{00022\ \textcolor{preprocessor}{\#include\ "{}\mbox{\hyperlink{time__utils_8h}{time\_utils.h}}"{}}}
\DoxyCodeLine{00023\ \textcolor{preprocessor}{\#include\ <stm32f4xx\_hal.h>}}
\DoxyCodeLine{00024\ }
\DoxyCodeLine{00031\ \textcolor{keyword}{typedef}\ \textcolor{keyword}{struct\ }\{}
\DoxyCodeLine{00032\ \ \ \ \ TIM\_HandleTypeDef\ *\mbox{\hyperlink{structencoder__t_ab261d27270a82f235db6c67840556fcb}{htim}};\ \ }
\DoxyCodeLine{00033\ \ \ \ \ int32\_t\ \mbox{\hyperlink{structencoder__t_a0fd6b4f8815c538a94db72846f3d88cd}{last\_count}};\ \ \ \ \ \ \ }
\DoxyCodeLine{00034\ \ \ \ \ int32\_t\ \mbox{\hyperlink{structencoder__t_a955921f275d4549d2e57f10cdef3bf45}{position}};\ \ \ \ \ \ \ \ \ }
\DoxyCodeLine{00035\ \ \ \ \ uint32\_t\ \mbox{\hyperlink{structencoder__t_a95021154678be1fe58b20ef8200d9f84}{last\_time\_us}};\ \ \ \ }
\DoxyCodeLine{00036\ \ \ \ \ int32\_t\ \mbox{\hyperlink{structencoder__t_a37a06f353c448694f29b00ce0126d4fb}{delta}};\ \ \ \ \ \ \ \ \ \ \ \ }
\DoxyCodeLine{00037\ \ \ \ \ \textcolor{keywordtype}{float}\ \mbox{\hyperlink{structencoder__t_a91c6fc842560bdd2ef14436c0135d4e6}{speed\_cps}};\ \ \ \ \ \ \ \ \ \ }
\DoxyCodeLine{00038\ \}\ \mbox{\hyperlink{structencoder__t}{encoder\_t}};}
\DoxyCodeLine{00039\ }
\DoxyCodeLine{00045\ \textcolor{keywordtype}{void}\ \mbox{\hyperlink{encoder_8h_a0d281a523aec02f31d4feb4bb3f35d51}{encoder\_init}}(\mbox{\hyperlink{structencoder__t}{encoder\_t}}\ *encoder,\ TIM\_HandleTypeDef\ *htim);}
\DoxyCodeLine{00046\ }
\DoxyCodeLine{00051\ \textcolor{keywordtype}{void}\ \mbox{\hyperlink{encoder_8h_a01f4459d7b34aebb118a13ab9f8a80ae}{encoder\_update}}(\mbox{\hyperlink{structencoder__t}{encoder\_t}}\ *encoder);}
\DoxyCodeLine{00052\ }
\DoxyCodeLine{00058\ int32\_t\ \mbox{\hyperlink{encoder_8h_a11e428db5d837a0db2d37f04a95e74e5}{encoder\_getposition}}(\mbox{\hyperlink{structencoder__t}{encoder\_t}}\ *encoder);}
\DoxyCodeLine{00059\ }
\DoxyCodeLine{00065\ int32\_t\ \mbox{\hyperlink{encoder_8h_a35cc8efb5877f4de74fae409748be0dc}{encoder\_getdelta}}(\mbox{\hyperlink{structencoder__t}{encoder\_t}}\ *encoder);}
\DoxyCodeLine{00066\ }
\DoxyCodeLine{00072\ \textcolor{keywordtype}{float}\ \mbox{\hyperlink{encoder_8h_a6b1ea1a649b4593daa55f65094db7f04}{encoder\_getspeed}}(\mbox{\hyperlink{structencoder__t}{encoder\_t}}\ *encoder);}
\DoxyCodeLine{00073\ }
\DoxyCodeLine{00078\ \textcolor{keywordtype}{void}\ \mbox{\hyperlink{encoder_8h_a839c6e77e921e4b73f91b67e141dd1ac}{encoder\_reset}}(\mbox{\hyperlink{structencoder__t}{encoder\_t}}\ *encoder);}
\DoxyCodeLine{00079\ }
\DoxyCodeLine{00080\ \textcolor{preprocessor}{\#ifdef\ \_\_cplusplus}}
\DoxyCodeLine{00081\ \}}
\DoxyCodeLine{00082\ \textcolor{preprocessor}{\#endif}}
\DoxyCodeLine{00083\ }
\DoxyCodeLine{00084\ \textcolor{preprocessor}{\#endif\ }\textcolor{comment}{/*\ INC\_ENCODER\_H\_\ */}\textcolor{preprocessor}{}}

\end{DoxyCode}

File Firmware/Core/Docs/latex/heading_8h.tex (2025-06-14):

\doxysection{Inc/heading.h File Reference}
\hypertarget{heading_8h}{}\label{heading_8h}\index{Inc/heading.h@{Inc/heading.h}}

FSM class for heading-\/based robot control using IMU input.  

{\ttfamily \#include "{}command\+\_\+parser.\+h"{}}\newline
{\ttfamily \#include "{}BNO055\+\_\+\+STM32.\+h"{}}\newline
{\ttfamily \#include "{}time\+\_\+utils.\+h"{}}\newline
{\ttfamily \#include $<$stdint.\+h$>$}\newline
{\ttfamily \#include $<$algorithm$>$}\newline
\doxysubsubsection*{Classes}
\begin{DoxyCompactItemize}
\item 
class \mbox{\hyperlink{class_h_e_a_d_i_n_g}{HEADING}}
\begin{DoxyCompactList}\small\item\em Finite State Machine for heading control based on IMU data. \end{DoxyCompactList}\end{DoxyCompactItemize}
\doxysubsubsection*{Variables}
\begin{DoxyCompactItemize}
\item 
COMMAND\+\_\+\+PARSER \mbox{\hyperlink{heading_8h_a166d58d7e5b485f50b066bb572d4e52d}{parser}}
\begin{DoxyCompactList}\small\item\em External reference to the command parser. \end{DoxyCompactList}\item 
\mbox{\hyperlink{struct_b_n_o055___sensors__t}{BNO055\+\_\+\+Sensors\+\_\+t}} \mbox{\hyperlink{heading_8h_a7871395ef24115844178e306695a6b39}{BNO055}}
\begin{DoxyCompactList}\small\item\em External reference to BNO055 IMU data structure. \end{DoxyCompactList}\item 
volatile bool \mbox{\hyperlink{heading_8h_a59cc8776b62c3d309d2ceafcfbfa504c}{USER}}
\begin{DoxyCompactList}\small\item\em External flag triggered by user button press. \end{DoxyCompactList}\end{DoxyCompactItemize}

\doxysubsection{Detailed Description}
FSM class for heading-\/based robot control using IMU input. 

Defines a finite state machine for maintaining or adjusting the robot\textquotesingle{}s heading based on IMU data and a heading setpoint received via parser. 

\label{doc-var-members}
\Hypertarget{heading_8h_doc-var-members}
\doxysubsection{Variable Documentation}
\Hypertarget{heading_8h_a7871395ef24115844178e306695a6b39}\index{heading.h@{heading.h}!BNO055@{BNO055}}
\index{BNO055@{BNO055}!heading.h@{heading.h}}
\doxysubsubsection{\texorpdfstring{BNO055}{BNO055}}
{\footnotesize\ttfamily \label{heading_8h_a7871395ef24115844178e306695a6b39} 
\mbox{\hyperlink{struct_b_n_o055___sensors__t}{BNO055\+\_\+\+Sensors\+\_\+t}} BNO055\hspace{0.3cm}{\ttfamily [extern]}}

External reference to BNO055 IMU data structure. 

External reference to BNO055 IMU data structure. \Hypertarget{heading_8h_a166d58d7e5b485f50b066bb572d4e52d}\index{heading.h@{heading.h}!parser@{parser}}
\index{parser@{parser}!heading.h@{heading.h}}
\doxysubsubsection{\texorpdfstring{parser}{parser}}
{\footnotesize\ttfamily \label{heading_8h_a166d58d7e5b485f50b066bb572d4e52d} 
COMMAND\+\_\+\+PARSER parser\hspace{0.3cm}{\ttfamily [extern]}}

External reference to the command parser. 

BNO055 data structure definition which hold euler, quaternion, linearaccel, gyro etc. parameters \Hypertarget{heading_8h_a59cc8776b62c3d309d2ceafcfbfa504c}\index{heading.h@{heading.h}!USER@{USER}}
\index{USER@{USER}!heading.h@{heading.h}}
\doxysubsubsection{\texorpdfstring{USER}{USER}}
{\footnotesize\ttfamily \label{heading_8h_a59cc8776b62c3d309d2ceafcfbfa504c} 
volatile bool USER\hspace{0.3cm}{\ttfamily [extern]}}

External flag triggered by user button press. 

External flag triggered by user button press.

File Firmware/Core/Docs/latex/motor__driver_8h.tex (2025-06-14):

\doxysection{Inc/motor\+\_\+driver.h File Reference}
\hypertarget{motor__driver_8h}{}\label{motor__driver_8h}\index{Inc/motor\_driver.h@{Inc/motor\_driver.h}}

Low-\/level motor control interface for STM32 using PWM.  

{\ttfamily \#include $<$stdio.\+h$>$}\newline
{\ttfamily \#include $<$stdint.\+h$>$}\newline
{\ttfamily \#include $<$stm32f4xx\+\_\+hal.\+h$>$}\newline
\doxysubsubsection*{Classes}
\begin{DoxyCompactItemize}
\item 
struct \mbox{\hyperlink{structmotor__t}{motor\+\_\+t}}
\begin{DoxyCompactList}\small\item\em Struct representing a DC motor controlled by two PWM channels. \end{DoxyCompactList}\end{DoxyCompactItemize}
\doxysubsubsection*{Functions}
\begin{DoxyCompactItemize}
\item 
void \mbox{\hyperlink{motor__driver_8h_a2f641758e0fa8e27d60ee59ece397f59}{motor\+\_\+set\+\_\+duty}} (\mbox{\hyperlink{structmotor__t}{motor\+\_\+t}} \texorpdfstring{$\ast$}{*}p\+\_\+mot, int32\+\_\+t duty)
\begin{DoxyCompactList}\small\item\em Sets the PWM duty cycle to control motor speed and direction. \end{DoxyCompactList}\item 
void \mbox{\hyperlink{motor__driver_8h_ace1968bd49ab675a540ed0d2edb4ac26}{motor\+\_\+enable}} (\mbox{\hyperlink{structmotor__t}{motor\+\_\+t}} \texorpdfstring{$\ast$}{*}p\+\_\+mot)
\begin{DoxyCompactList}\small\item\em Enables PWM output to the motor by starting both channels. \end{DoxyCompactList}\item 
void \mbox{\hyperlink{motor__driver_8h_a1f6976479a67dcb435a19de74c5d6e60}{motor\+\_\+disable}} (\mbox{\hyperlink{structmotor__t}{motor\+\_\+t}} \texorpdfstring{$\ast$}{*}p\+\_\+mot)
\begin{DoxyCompactList}\small\item\em Disables PWM output to the motor. \end{DoxyCompactList}\end{DoxyCompactItemize}

\doxysubsection{Detailed Description}
Low-\/level motor control interface for STM32 using PWM. 

Defines the motor object and provides function prototypes to control motor direction and speed through timer-\/based PWM outputs. 

\label{doc-func-members}
\Hypertarget{motor__driver_8h_doc-func-members}
\doxysubsection{Function Documentation}
\Hypertarget{motor__driver_8h_a1f6976479a67dcb435a19de74c5d6e60}\index{motor\_driver.h@{motor\_driver.h}!motor\_disable@{motor\_disable}}
\index{motor\_disable@{motor\_disable}!motor\_driver.h@{motor\_driver.h}}
\doxysubsubsection{\texorpdfstring{motor\_disable()}{motor\_disable()}}
{\footnotesize\ttfamily \label{motor__driver_8h_a1f6976479a67dcb435a19de74c5d6e60} 
void motor\+\_\+disable (\begin{DoxyParamCaption}\item[{\mbox{\hyperlink{structmotor__t}{motor\+\_\+t}} \texorpdfstring{$\ast$}{*}}]{p\+\_\+mot}{}\end{DoxyParamCaption})}

Disables PWM output to the motor. 

\begin{DoxyParams}{Parameters}
{\em p\+\_\+mot} & Pointer to motor object.\\
\hline
\end{DoxyParams}
Disables PWM output to the motor.

\begin{DoxyParams}{Parameters}
{\em p\+\_\+mot} & Pointer to motor object to disable.\\
\hline
\end{DoxyParams}
Stops the timer\textquotesingle{}s PWM outputs on the assigned motor channels. \Hypertarget{motor__driver_8h_ace1968bd49ab675a540ed0d2edb4ac26}\index{motor\_driver.h@{motor\_driver.h}!motor\_enable@{motor\_enable}}
\index{motor\_enable@{motor\_enable}!motor\_driver.h@{motor\_driver.h}}
\doxysubsubsection{\texorpdfstring{motor\_enable()}{motor\_enable()}}
{\footnotesize\ttfamily \label{motor__driver_8h_ace1968bd49ab675a540ed0d2edb4ac26} 
void motor\+\_\+enable (\begin{DoxyParamCaption}\item[{\mbox{\hyperlink{structmotor__t}{motor\+\_\+t}} \texorpdfstring{$\ast$}{*}}]{p\+\_\+mot}{}\end{DoxyParamCaption})}

Enables PWM output to the motor by starting both channels. 

\begin{DoxyParams}{Parameters}
{\em p\+\_\+mot} & Pointer to motor object.\\
\hline
\end{DoxyParams}
Enables PWM output to the motor by starting both channels.

\begin{DoxyParams}{Parameters}
{\em p\+\_\+mot} & Pointer to motor object to enable.\\
\hline
\end{DoxyParams}
Starts the timer\textquotesingle{}s PWM outputs on the assigned motor channels. \Hypertarget{motor__driver_8h_a2f641758e0fa8e27d60ee59ece397f59}\index{motor\_driver.h@{motor\_driver.h}!motor\_set\_duty@{motor\_set\_duty}}
\index{motor\_set\_duty@{motor\_set\_duty}!motor\_driver.h@{motor\_driver.h}}
\doxysubsubsection{\texorpdfstring{motor\_set\_duty()}{motor\_set\_duty()}}
{\footnotesize\ttfamily \label{motor__driver_8h_a2f641758e0fa8e27d60ee59ece397f59} 
void motor\+\_\+set\+\_\+duty (\begin{DoxyParamCaption}\item[{\mbox{\hyperlink{structmotor__t}{motor\+\_\+t}} \texorpdfstring{$\ast$}{*}}]{p\+\_\+mot}{, }\item[{int32\+\_\+t}]{duty}{}\end{DoxyParamCaption})}

Sets the PWM duty cycle to control motor speed and direction. 

\begin{DoxyParams}{Parameters}
{\em p\+\_\+mot} & Pointer to motor object. \\
\hline
{\em duty} & Signed duty cycle (-\/timer period to +timer period).\\
\hline
\end{DoxyParams}
Sets the PWM duty cycle to control motor speed and direction.

\begin{DoxyParams}{Parameters}
{\em p\+\_\+mot} & Pointer to motor object. \\
\hline
{\em duty} & Signed value representing the duty cycle (positive = forward, negative = reverse).\\
\hline
\end{DoxyParams}
Saturates the input duty cycle to match the timer auto-\/reload (ARR) value. Enforces a deadzone below which effort is ignored. Uses two complementary PWM channels to drive H-\/bridge outputs.

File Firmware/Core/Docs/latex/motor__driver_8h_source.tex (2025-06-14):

\doxysection{motor\+\_\+driver.\+h}
\hypertarget{motor__driver_8h_source}{}\label{motor__driver_8h_source}\index{Inc/motor\_driver.h@{Inc/motor\_driver.h}}
\mbox{\hyperlink{motor__driver_8h}{Go to the documentation of this file.}}
\begin{DoxyCode}{0}
\DoxyCodeLine{00001\ \textcolor{comment}{/*}}
\DoxyCodeLine{00002\ \textcolor{comment}{\ *\ motor\_driver.h}}
\DoxyCodeLine{00003\ \textcolor{comment}{\ *}}
\DoxyCodeLine{00004\ \textcolor{comment}{\ *\ \ Created\ on:\ Apr\ 17,\ 2025}}
\DoxyCodeLine{00005\ \textcolor{comment}{\ *\ \ \ \ \ \ Author:\ jacka}}
\DoxyCodeLine{00006\ \textcolor{comment}{\ */}}
\DoxyCodeLine{00007\ }
\DoxyCodeLine{00008\ \textcolor{preprocessor}{\#ifndef\ INC\_MOTOR\_DRIVER\_H\_}}
\DoxyCodeLine{00009\ \textcolor{preprocessor}{\#define\ INC\_MOTOR\_DRIVER\_H\_}}
\DoxyCodeLine{00010\ }
\DoxyCodeLine{00017\ }
\DoxyCodeLine{00018\ \textcolor{preprocessor}{\#ifdef\ \_\_cplusplus}}
\DoxyCodeLine{00019\ \textcolor{keyword}{extern}\ \textcolor{stringliteral}{"{}C"{}}\ \{}
\DoxyCodeLine{00020\ \textcolor{preprocessor}{\#endif}}
\DoxyCodeLine{00021\ }
\DoxyCodeLine{00022\ \textcolor{preprocessor}{\#include\ <stdio.h>}}
\DoxyCodeLine{00023\ \textcolor{preprocessor}{\#include\ <stdint.h>}}
\DoxyCodeLine{00024\ \textcolor{preprocessor}{\#include\ <stm32f4xx\_hal.h>}\ \textcolor{comment}{//\ Include\ HAL\ functions}}
\DoxyCodeLine{00025\ }
\DoxyCodeLine{00031\ \textcolor{keyword}{typedef}\ \textcolor{keyword}{struct\ }\{}
\DoxyCodeLine{00032\ \ \ \ \ int32\_t\ \ \mbox{\hyperlink{structmotor__t_a856e42e815289c9e2a05f9f50183f9b0}{duty}};\ \ \ \ \ \ \ \ \ \ \ \ \ \ }
\DoxyCodeLine{00033\ \ \ \ \ TIM\_HandleTypeDef*\ \mbox{\hyperlink{structmotor__t_a773d5dfb4db57609948b961bbfec6197}{htim}};\ \ \ \ }
\DoxyCodeLine{00034\ \ \ \ \ uint32\_t\ \mbox{\hyperlink{structmotor__t_a7ab9baa95a5d0c1832a14b45b80b5a73}{ch\_A}};\ \ \ \ \ \ \ \ \ \ \ \ \ \ }
\DoxyCodeLine{00035\ \ \ \ \ uint32\_t\ \mbox{\hyperlink{structmotor__t_a78c87ae23f6a4d6234ecd9e989e3dc2b}{ch\_B}};\ \ \ \ \ \ \ \ \ \ \ \ \ \ }
\DoxyCodeLine{00036\ \}\ \mbox{\hyperlink{structmotor__t}{motor\_t}};}
\DoxyCodeLine{00037\ }
\DoxyCodeLine{00043\ \textcolor{keywordtype}{void}\ \mbox{\hyperlink{motor__driver_8h_a2f641758e0fa8e27d60ee59ece397f59}{motor\_set\_duty}}(\mbox{\hyperlink{structmotor__t}{motor\_t}}*\ p\_mot,\ int32\_t\ duty);}
\DoxyCodeLine{00044\ }
\DoxyCodeLine{00049\ \textcolor{keywordtype}{void}\ \mbox{\hyperlink{motor__driver_8h_ace1968bd49ab675a540ed0d2edb4ac26}{motor\_enable}}(\mbox{\hyperlink{structmotor__t}{motor\_t}}*\ p\_mot);}
\DoxyCodeLine{00050\ }
\DoxyCodeLine{00055\ \textcolor{keywordtype}{void}\ \mbox{\hyperlink{motor__driver_8h_a1f6976479a67dcb435a19de74c5d6e60}{motor\_disable}}(\mbox{\hyperlink{structmotor__t}{motor\_t}}*\ p\_mot);}
\DoxyCodeLine{00056\ }
\DoxyCodeLine{00057\ \textcolor{preprocessor}{\#ifdef\ \_\_cplusplus}}
\DoxyCodeLine{00058\ \}}
\DoxyCodeLine{00059\ \textcolor{preprocessor}{\#endif}}
\DoxyCodeLine{00060\ }
\DoxyCodeLine{00061\ \textcolor{preprocessor}{\#endif\ }\textcolor{comment}{/*\ INC\_MOTOR\_DRIVER\_H\_\ */}\textcolor{preprocessor}{}}

\end{DoxyCode}

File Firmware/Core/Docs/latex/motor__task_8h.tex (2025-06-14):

\doxysection{Inc/motor\+\_\+task.h File Reference}
\hypertarget{motor__task_8h}{}\label{motor__task_8h}\index{Inc/motor\_task.h@{Inc/motor\_task.h}}

Motor control task with feedback and coordination logic.  

{\ttfamily \#include "{}motor\+\_\+driver.\+h"{}}\newline
{\ttfamily \#include "{}encoder.\+h"{}}\newline
{\ttfamily \#include "{}bluetooth.\+h"{}}\newline
{\ttfamily \#include "{}command\+\_\+parser.\+h"{}}\newline
{\ttfamily \#include "{}heading.\+h"{}}\newline
{\ttfamily \#include "{}balance.\+h"{}}\newline
{\ttfamily \#include "{}time\+\_\+utils.\+h"{}}\newline
{\ttfamily \#include $<$stdint.\+h$>$}\newline
{\ttfamily \#include $<$algorithm$>$}\newline
\doxysubsubsection*{Classes}
\begin{DoxyCompactItemize}
\item 
class \mbox{\hyperlink{class_m_o_t_o_r___t_a_s_k}{MOTOR\+\_\+\+TASK}}
\begin{DoxyCompactList}\small\item\em Finite State Machine for low-\/level motor control. \end{DoxyCompactList}\end{DoxyCompactItemize}
\doxysubsubsection*{Variables}
\begin{DoxyCompactItemize}
\item 
\Hypertarget{motor__task_8h_a25fc663547539bc49fecc0011bd76ab5}\label{motor__task_8h_a25fc663547539bc49fecc0011bd76ab5} 
TIM\+\_\+\+Handle\+Type\+Def {\bfseries htim1}
\begin{DoxyCompactList}\small\item\em Timer handle for PWM generation on motor 1. \end{DoxyCompactList}\item 
\Hypertarget{motor__task_8h_aac3d2c59ee0e3bbae1b99529a154eb62}\label{motor__task_8h_aac3d2c59ee0e3bbae1b99529a154eb62} 
TIM\+\_\+\+Handle\+Type\+Def {\bfseries htim3}
\begin{DoxyCompactList}\small\item\em Timer handle for encoder 1 (e.\+g., left wheel). \end{DoxyCompactList}\item 
\Hypertarget{motor__task_8h_a85788cec5a97ee377e4ee2e74f026484}\label{motor__task_8h_a85788cec5a97ee377e4ee2e74f026484} 
TIM\+\_\+\+Handle\+Type\+Def {\bfseries htim4}
\begin{DoxyCompactList}\small\item\em Timer handle for encoder 2 (e.\+g., right wheel). \end{DoxyCompactList}\item 
\Hypertarget{motor__task_8h_acefaeaaa3856ddddae7083b2d220fe4b}\label{motor__task_8h_acefaeaaa3856ddddae7083b2d220fe4b} 
TIM\+\_\+\+Handle\+Type\+Def {\bfseries htim5}
\begin{DoxyCompactList}\small\item\em Timer handle for motor 2 PWM generation. \end{DoxyCompactList}\item 
\Hypertarget{motor__task_8h_a9b790b620dceefcde3befffb66864e08}\label{motor__task_8h_a9b790b620dceefcde3befffb66864e08} 
\mbox{\hyperlink{class_b_l_u_e_t_o_o_t_h}{BLUETOOTH}} {\bfseries bluetooth}
\begin{DoxyCompactList}\small\item\em Global reference to Bluetooth control FSM. \end{DoxyCompactList}\item 
COMMAND\+\_\+\+PARSER \mbox{\hyperlink{motor__task_8h_a166d58d7e5b485f50b066bb572d4e52d}{parser}}
\begin{DoxyCompactList}\small\item\em Global reference to UART command parser. \end{DoxyCompactList}\item 
\Hypertarget{motor__task_8h_ac620a20633fa0122af674367e4ea4baa}\label{motor__task_8h_ac620a20633fa0122af674367e4ea4baa} 
\mbox{\hyperlink{class_h_e_a_d_i_n_g}{HEADING}} {\bfseries heading}
\begin{DoxyCompactList}\small\item\em Global reference to heading control task. \end{DoxyCompactList}\item 
\Hypertarget{motor__task_8h_af3f7ab56056a228ea9e41b6a599ceaa3}\label{motor__task_8h_af3f7ab56056a228ea9e41b6a599ceaa3} 
\mbox{\hyperlink{class_b_a_l_a_n_c_e}{BALANCE}} {\bfseries balance}
\begin{DoxyCompactList}\small\item\em Global reference to balance control task. \end{DoxyCompactList}\item 
\Hypertarget{motor__task_8h_ab6bdf79e02c3ccb3b22efe8fb44d1818}\label{motor__task_8h_ab6bdf79e02c3ccb3b22efe8fb44d1818} 
int32\+\_\+t {\bfseries AR}
\begin{DoxyCompactList}\small\item\em Global auto-\/reload value for timers. \end{DoxyCompactList}\end{DoxyCompactItemize}

\doxysubsection{Detailed Description}
Motor control task with feedback and coordination logic. 

Defines the \doxylink{class_m_o_t_o_r___t_a_s_k}{MOTOR\+\_\+\+TASK} class, which uses encoder feedback and setpoints from various control modules (Bluetooth, Heading, Balance) to regulate motor speed and direction using PID control. 

\label{doc-var-members}
\Hypertarget{motor__task_8h_doc-var-members}
\doxysubsection{Variable Documentation}
\Hypertarget{motor__task_8h_a166d58d7e5b485f50b066bb572d4e52d}\index{motor\_task.h@{motor\_task.h}!parser@{parser}}
\index{parser@{parser}!motor\_task.h@{motor\_task.h}}
\doxysubsubsection{\texorpdfstring{parser}{parser}}
{\footnotesize\ttfamily \label{motor__task_8h_a166d58d7e5b485f50b066bb572d4e52d} 
COMMAND\+\_\+\+PARSER parser\hspace{0.3cm}{\ttfamily [extern]}}

Global reference to UART command parser. 

Global reference to UART command parser.

BNO055 data structure definition which hold euler, quaternion, linearaccel, gyro etc. parameters

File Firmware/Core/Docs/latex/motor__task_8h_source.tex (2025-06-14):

\doxysection{motor\+\_\+task.\+h}
\hypertarget{motor__task_8h_source}{}\label{motor__task_8h_source}\index{Inc/motor\_task.h@{Inc/motor\_task.h}}
\mbox{\hyperlink{motor__task_8h}{Go to the documentation of this file.}}
\begin{DoxyCode}{0}
\DoxyCodeLine{00001\ \textcolor{comment}{/*}}
\DoxyCodeLine{00002\ \textcolor{comment}{\ *\ motor\_task.h}}
\DoxyCodeLine{00003\ \textcolor{comment}{\ *}}
\DoxyCodeLine{00004\ \textcolor{comment}{\ *\ \ Created\ on:\ Jun\ 2,\ 2025}}
\DoxyCodeLine{00005\ \textcolor{comment}{\ *\ \ \ \ \ \ Author:\ jacka}}
\DoxyCodeLine{00006\ \textcolor{comment}{\ */}}
\DoxyCodeLine{00007\ }
\DoxyCodeLine{00008\ \textcolor{preprocessor}{\#ifndef\ INC\_MOTOR\_TASK\_H\_}}
\DoxyCodeLine{00009\ \textcolor{preprocessor}{\#define\ INC\_MOTOR\_TASK\_H\_}}
\DoxyCodeLine{00010\ }
\DoxyCodeLine{00018\ }
\DoxyCodeLine{00019\ \textcolor{preprocessor}{\#include\ "{}\mbox{\hyperlink{motor__driver_8h}{motor\_driver.h}}"{}}}
\DoxyCodeLine{00020\ \textcolor{preprocessor}{\#include\ "{}\mbox{\hyperlink{encoder_8h}{encoder.h}}"{}}}
\DoxyCodeLine{00021\ \textcolor{preprocessor}{\#include\ "{}\mbox{\hyperlink{bluetooth_8h}{bluetooth.h}}"{}}}
\DoxyCodeLine{00022\ \textcolor{preprocessor}{\#include\ "{}\mbox{\hyperlink{command__parser_8h}{command\_parser.h}}"{}}}
\DoxyCodeLine{00023\ \textcolor{preprocessor}{\#include\ "{}\mbox{\hyperlink{heading_8h}{heading.h}}"{}}}
\DoxyCodeLine{00024\ \textcolor{preprocessor}{\#include\ "{}\mbox{\hyperlink{balance_8h}{balance.h}}"{}}}
\DoxyCodeLine{00025\ \textcolor{preprocessor}{\#include\ "{}\mbox{\hyperlink{time__utils_8h}{time\_utils.h}}"{}}}
\DoxyCodeLine{00026\ \textcolor{preprocessor}{\#include\ <stdint.h>}}
\DoxyCodeLine{00027\ \textcolor{preprocessor}{\#include\ <algorithm>}}
\DoxyCodeLine{00028\ }
\DoxyCodeLine{00030\ \textcolor{keyword}{extern}\ TIM\_HandleTypeDef\ \mbox{\hyperlink{motor__task_8h_a25fc663547539bc49fecc0011bd76ab5}{htim1}};}
\DoxyCodeLine{00032\ \textcolor{keyword}{extern}\ TIM\_HandleTypeDef\ \mbox{\hyperlink{motor__task_8h_aac3d2c59ee0e3bbae1b99529a154eb62}{htim3}};}
\DoxyCodeLine{00034\ \textcolor{keyword}{extern}\ TIM\_HandleTypeDef\ \mbox{\hyperlink{motor__task_8h_a85788cec5a97ee377e4ee2e74f026484}{htim4}};}
\DoxyCodeLine{00036\ \textcolor{keyword}{extern}\ TIM\_HandleTypeDef\ \mbox{\hyperlink{motor__task_8h_acefaeaaa3856ddddae7083b2d220fe4b}{htim5}};}
\DoxyCodeLine{00037\ }
\DoxyCodeLine{00039\ \textcolor{keyword}{extern}\ \mbox{\hyperlink{class_b_l_u_e_t_o_o_t_h}{BLUETOOTH}}\ \mbox{\hyperlink{motor__task_8h_a9b790b620dceefcde3befffb66864e08}{bluetooth}};}
\DoxyCodeLine{00040\ }
\DoxyCodeLine{00042\ \textcolor{keyword}{extern}\ COMMAND\_PARSER\ \mbox{\hyperlink{heading_8h_a166d58d7e5b485f50b066bb572d4e52d}{parser}};}
\DoxyCodeLine{00043\ }
\DoxyCodeLine{00045\ \textcolor{keyword}{extern}\ \mbox{\hyperlink{class_h_e_a_d_i_n_g}{HEADING}}\ \mbox{\hyperlink{motor__task_8h_ac620a20633fa0122af674367e4ea4baa}{heading}};}
\DoxyCodeLine{00046\ }
\DoxyCodeLine{00048\ \textcolor{keyword}{extern}\ \mbox{\hyperlink{class_b_a_l_a_n_c_e}{BALANCE}}\ \mbox{\hyperlink{motor__task_8h_af3f7ab56056a228ea9e41b6a599ceaa3}{balance}};}
\DoxyCodeLine{00049\ }
\DoxyCodeLine{00051\ \textcolor{keyword}{extern}\ int32\_t\ \mbox{\hyperlink{motor__task_8h_ab6bdf79e02c3ccb3b22efe8fb44d1818}{AR}};}
\DoxyCodeLine{00052\ }
\DoxyCodeLine{00059\ \textcolor{keyword}{class\ }\mbox{\hyperlink{class_m_o_t_o_r___t_a_s_k_ae26d0eb531047dbe9138db9fdfa3e919}{MOTOR\_TASK}}}
\DoxyCodeLine{00060\ \{}
\DoxyCodeLine{00061\ \textcolor{keyword}{public}:}
\DoxyCodeLine{00066\ \ \ \ \ \textcolor{keyword}{typedef}\ \textcolor{keyword}{enum}\ \mbox{\hyperlink{class_m_o_t_o_r___t_a_s_k_a6d75db7139226796bf367ad21532764e}{state}}}
\DoxyCodeLine{00067\ \ \ \ \ \{}
\DoxyCodeLine{00068\ \ \ \ \ \ \ \ \ \mbox{\hyperlink{class_m_o_t_o_r___t_a_s_k_a6d75db7139226796bf367ad21532764eaef9cab90e249ed385da6f46cebea30a5}{S0\_INIT}},\ \ }
\DoxyCodeLine{00069\ \ \ \ \ \ \ \ \ \mbox{\hyperlink{class_m_o_t_o_r___t_a_s_k_a6d75db7139226796bf367ad21532764eae176dfa4e642ce0fdebe3e2f3a8c637f}{S1\_IDLE}},\ \ }
\DoxyCodeLine{00070\ \ \ \ \ \ \ \ \ \mbox{\hyperlink{class_m_o_t_o_r___t_a_s_k_a6d75db7139226796bf367ad21532764eaa6081173e732510f654678a1c39eda63}{S2\_RUN}}\ \ \ \ }
\DoxyCodeLine{00071\ \ \ \ \ \}\ state\_t;}
\DoxyCodeLine{00072\ }
\DoxyCodeLine{00076\ \ \ \ \ \mbox{\hyperlink{class_m_o_t_o_r___t_a_s_k_ae26d0eb531047dbe9138db9fdfa3e919}{MOTOR\_TASK}}();}
\DoxyCodeLine{00077\ }
\DoxyCodeLine{00082\ \ \ \ \ \textcolor{keywordtype}{void}\ \mbox{\hyperlink{class_m_o_t_o_r___t_a_s_k_a5f7351d0feb13b529c1589a9e4108a49}{run}}(\textcolor{keywordtype}{void});}
\DoxyCodeLine{00083\ }
\DoxyCodeLine{00084\ \textcolor{keyword}{private}:}
\DoxyCodeLine{00085\ \ \ \ \ state\_t\ \mbox{\hyperlink{class_m_o_t_o_r___t_a_s_k_a6d75db7139226796bf367ad21532764e}{state}};\ \ \ \ \ \ \ }
\DoxyCodeLine{00086\ \ \ \ \ \textcolor{keywordtype}{bool}\ should\_run();\ \ \ }
\DoxyCodeLine{00087\ }
\DoxyCodeLine{00088\ \ \ \ \ \textcolor{comment}{//\ Motor\ hardware\ abstraction}}
\DoxyCodeLine{00089\ \ \ \ \ \mbox{\hyperlink{structmotor__t}{motor\_t}}\ motor1;\ \ \ \ \ \ }
\DoxyCodeLine{00090\ \ \ \ \ \mbox{\hyperlink{structmotor__t}{motor\_t}}\ motor2;\ \ \ \ \ \ }
\DoxyCodeLine{00091\ }
\DoxyCodeLine{00092\ \ \ \ \ \textcolor{keywordtype}{float}\ M1\_eff;\ \ \ \ \ \ \ \ }
\DoxyCodeLine{00093\ \ \ \ \ \textcolor{keywordtype}{float}\ M2\_eff;\ \ \ \ \ \ \ \ }
\DoxyCodeLine{00094\ }
\DoxyCodeLine{00095\ \ \ \ \ int16\_t\ M1\_set;\ \ \ \ \ \ }
\DoxyCodeLine{00096\ \ \ \ \ int16\_t\ M2\_set;\ \ \ \ \ \ }
\DoxyCodeLine{00097\ }
\DoxyCodeLine{00098\ \ \ \ \ \textcolor{comment}{//\ Encoder\ feedback}}
\DoxyCodeLine{00099\ \ \ \ \ \mbox{\hyperlink{structencoder__t}{encoder\_t}}\ encoder1;\ \ }
\DoxyCodeLine{00100\ \ \ \ \ \mbox{\hyperlink{structencoder__t}{encoder\_t}}\ encoder2;\ \ }
\DoxyCodeLine{00101\ }
\DoxyCodeLine{00102\ \ \ \ \ \textcolor{comment}{//\ PID\ gains\ for\ motor\ 1}}
\DoxyCodeLine{00103\ \ \ \ \ \textcolor{keywordtype}{float}\ Kp1;\ \ \ \ \ \ \ \ \ \ \ }
\DoxyCodeLine{00104\ \ \ \ \ \textcolor{keywordtype}{float}\ Ki1;\ \ \ \ \ \ \ \ \ \ \ }
\DoxyCodeLine{00105\ \ \ \ \ \textcolor{keywordtype}{float}\ Kd1;\ \ \ \ \ \ \ \ \ \ \ }
\DoxyCodeLine{00106\ }
\DoxyCodeLine{00107\ \ \ \ \ \textcolor{comment}{//\ PID\ state\ variables\ for\ motor\ 1}}
\DoxyCodeLine{00108\ \ \ \ \ int32\_t\ error1;}
\DoxyCodeLine{00109\ \ \ \ \ int32\_t\ prev\_error1;}
\DoxyCodeLine{00110\ \ \ \ \ int32\_t\ error\_diff1;}
\DoxyCodeLine{00111\ \ \ \ \ int32\_t\ error\_sum1;}
\DoxyCodeLine{00112\ }
\DoxyCodeLine{00113\ \ \ \ \ \textcolor{comment}{//\ PID\ gains\ for\ motor\ 2}}
\DoxyCodeLine{00114\ \ \ \ \ \textcolor{keywordtype}{float}\ Kp2;}
\DoxyCodeLine{00115\ \ \ \ \ \textcolor{keywordtype}{float}\ Ki2;}
\DoxyCodeLine{00116\ \ \ \ \ \textcolor{keywordtype}{float}\ Kd2;}
\DoxyCodeLine{00117\ }
\DoxyCodeLine{00118\ \ \ \ \ \textcolor{comment}{//\ PID\ state\ variables\ for\ motor\ 2}}
\DoxyCodeLine{00119\ \ \ \ \ int32\_t\ error2;}
\DoxyCodeLine{00120\ \ \ \ \ int32\_t\ prev\_error2;}
\DoxyCodeLine{00121\ \ \ \ \ int32\_t\ error\_diff2;}
\DoxyCodeLine{00122\ \ \ \ \ int32\_t\ error\_sum2;}
\DoxyCodeLine{00123\ }
\DoxyCodeLine{00124\ \ \ \ \ \textcolor{comment}{//\ Timing\ variables}}
\DoxyCodeLine{00125\ \ \ \ \ uint32\_t\ dt;\ \ \ \ \ \ \ \ \ }
\DoxyCodeLine{00126\ \ \ \ \ uint32\_t\ now;\ \ \ \ \ \ \ \ }
\DoxyCodeLine{00127\ \ \ \ \ uint32\_t\ last\_time;\ \ }
\DoxyCodeLine{00128\ \};}
\DoxyCodeLine{00129\ }
\DoxyCodeLine{00130\ \textcolor{preprocessor}{\#endif\ }\textcolor{comment}{/*\ INC\_MOTOR\_TASK\_H\_\ */}\textcolor{preprocessor}{}}

\end{DoxyCode}

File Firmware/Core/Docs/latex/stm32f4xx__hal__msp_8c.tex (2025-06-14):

\doxysection{Src/stm32f4xx\+\_\+hal\+\_\+msp.c File Reference}
\hypertarget{stm32f4xx__hal__msp_8c}{}\label{stm32f4xx__hal__msp_8c}\index{Src/stm32f4xx\_hal\_msp.c@{Src/stm32f4xx\_hal\_msp.c}}

This file provides code for the MSP Initialization and de-\/\+Initialization codes.  

{\ttfamily \#include "{}main.\+h"{}}\newline
\doxysubsubsection*{Functions}
\begin{DoxyCompactItemize}
\item 
void \mbox{\hyperlink{stm32f4xx__hal__msp_8c_ae70bce6c39d0b570a7523b86738cec4b}{HAL\+\_\+\+TIM\+\_\+\+Msp\+Post\+Init}} (TIM\+\_\+\+Handle\+Type\+Def \texorpdfstring{$\ast$}{*}htim)
\item 
void \mbox{\hyperlink{stm32f4xx__hal__msp_8c_ae4fb8e66865c87d0ebab74a726a6891f}{HAL\+\_\+\+Msp\+Init}} (void)
\item 
void \mbox{\hyperlink{stm32f4xx__hal__msp_8c_aa30863492d5c3103e3e8ce8a63dadd07}{HAL\+\_\+\+ADC\+\_\+\+Msp\+Init}} (ADC\+\_\+\+Handle\+Type\+Def \texorpdfstring{$\ast$}{*}hadc)
\begin{DoxyCompactList}\small\item\em ADC MSP Initialization This function configures the hardware resources used in this example. \end{DoxyCompactList}\item 
void \mbox{\hyperlink{stm32f4xx__hal__msp_8c_a39b0f8e80268ab3e660ead921ad4b22f}{HAL\+\_\+\+ADC\+\_\+\+Msp\+De\+Init}} (ADC\+\_\+\+Handle\+Type\+Def \texorpdfstring{$\ast$}{*}hadc)
\begin{DoxyCompactList}\small\item\em ADC MSP De-\/\+Initialization This function freeze the hardware resources used in this example. \end{DoxyCompactList}\item 
void \mbox{\hyperlink{stm32f4xx__hal__msp_8c_abe01a202c27b23fc150aa66af3130073}{HAL\+\_\+\+I2\+C\+\_\+\+Msp\+Init}} (I2\+C\+\_\+\+Handle\+Type\+Def \texorpdfstring{$\ast$}{*}hi2c)
\begin{DoxyCompactList}\small\item\em I2C MSP Initialization This function configures the hardware resources used in this example. \end{DoxyCompactList}\item 
void \mbox{\hyperlink{stm32f4xx__hal__msp_8c_a2ec8d9b09854c732e2feed549278f048}{HAL\+\_\+\+I2\+C\+\_\+\+Msp\+De\+Init}} (I2\+C\+\_\+\+Handle\+Type\+Def \texorpdfstring{$\ast$}{*}hi2c)
\begin{DoxyCompactList}\small\item\em I2C MSP De-\/\+Initialization This function freeze the hardware resources used in this example. \end{DoxyCompactList}\item 
void \mbox{\hyperlink{stm32f4xx__hal__msp_8c_a24d5b9c609d8b753d95508419f4c1901}{HAL\+\_\+\+TIM\+\_\+\+PWM\+\_\+\+Msp\+Init}} (TIM\+\_\+\+Handle\+Type\+Def \texorpdfstring{$\ast$}{*}htim\+\_\+pwm)
\begin{DoxyCompactList}\small\item\em TIM\+\_\+\+PWM MSP Initialization This function configures the hardware resources used in this example. \end{DoxyCompactList}\item 
void \mbox{\hyperlink{stm32f4xx__hal__msp_8c_abb25ade2f7e3f7aae167bd52270c2b86}{HAL\+\_\+\+TIM\+\_\+\+Base\+\_\+\+Msp\+Init}} (TIM\+\_\+\+Handle\+Type\+Def \texorpdfstring{$\ast$}{*}htim\+\_\+base)
\begin{DoxyCompactList}\small\item\em TIM\+\_\+\+Base MSP Initialization This function configures the hardware resources used in this example. \end{DoxyCompactList}\item 
void \mbox{\hyperlink{stm32f4xx__hal__msp_8c_a8cc723aedb4c01bc57cbe38c21f0b0a3}{HAL\+\_\+\+TIM\+\_\+\+Encoder\+\_\+\+Msp\+Init}} (TIM\+\_\+\+Handle\+Type\+Def \texorpdfstring{$\ast$}{*}htim\+\_\+encoder)
\begin{DoxyCompactList}\small\item\em TIM\+\_\+\+Encoder MSP Initialization This function configures the hardware resources used in this example. \end{DoxyCompactList}\item 
void \mbox{\hyperlink{stm32f4xx__hal__msp_8c_af5f524564b3a99a9f87f45227309e866}{HAL\+\_\+\+TIM\+\_\+\+PWM\+\_\+\+Msp\+De\+Init}} (TIM\+\_\+\+Handle\+Type\+Def \texorpdfstring{$\ast$}{*}htim\+\_\+pwm)
\begin{DoxyCompactList}\small\item\em TIM\+\_\+\+PWM MSP De-\/\+Initialization This function freeze the hardware resources used in this example. \end{DoxyCompactList}\item 
void \mbox{\hyperlink{stm32f4xx__hal__msp_8c_a555b8a2d3c7a07341f8cb1255318fa2b}{HAL\+\_\+\+TIM\+\_\+\+Base\+\_\+\+Msp\+De\+Init}} (TIM\+\_\+\+Handle\+Type\+Def \texorpdfstring{$\ast$}{*}htim\+\_\+base)
\begin{DoxyCompactList}\small\item\em TIM\+\_\+\+Base MSP De-\/\+Initialization This function freeze the hardware resources used in this example. \end{DoxyCompactList}\item 
void \mbox{\hyperlink{stm32f4xx__hal__msp_8c_a9a53eee786f7e7e0217ce5b466c75f8a}{HAL\+\_\+\+TIM\+\_\+\+Encoder\+\_\+\+Msp\+De\+Init}} (TIM\+\_\+\+Handle\+Type\+Def \texorpdfstring{$\ast$}{*}htim\+\_\+encoder)
\begin{DoxyCompactList}\small\item\em TIM\+\_\+\+Encoder MSP De-\/\+Initialization This function freeze the hardware resources used in this example. \end{DoxyCompactList}\item 
void \mbox{\hyperlink{stm32f4xx__hal__msp_8c_a0e553b32211877322f949b14801bbfa7}{HAL\+\_\+\+UART\+\_\+\+Msp\+Init}} (UART\+\_\+\+Handle\+Type\+Def \texorpdfstring{$\ast$}{*}huart)
\begin{DoxyCompactList}\small\item\em UART MSP Initialization This function configures the hardware resources used in this example. \end{DoxyCompactList}\item 
void \mbox{\hyperlink{stm32f4xx__hal__msp_8c_a718f39804e3b910d738a0e1e46151188}{HAL\+\_\+\+UART\+\_\+\+Msp\+De\+Init}} (UART\+\_\+\+Handle\+Type\+Def \texorpdfstring{$\ast$}{*}huart)
\begin{DoxyCompactList}\small\item\em UART MSP De-\/\+Initialization This function freeze the hardware resources used in this example. \end{DoxyCompactList}\end{DoxyCompactItemize}
\doxysubsubsection*{Variables}
\begin{DoxyCompactItemize}
\item 
\Hypertarget{stm32f4xx__hal__msp_8c_a784aa25dc7e4580cfbf80658340f482c}\label{stm32f4xx__hal__msp_8c_a784aa25dc7e4580cfbf80658340f482c} 
DMA\+\_\+\+Handle\+Type\+Def {\bfseries hdma\+\_\+usart2\+\_\+rx}
\end{DoxyCompactItemize}

\doxysubsection{Detailed Description}
This file provides code for the MSP Initialization and de-\/\+Initialization codes. 

\begin{DoxyAttention}{Attention}

\end{DoxyAttention}
Copyright (c) 2025 STMicroelectronics. All rights reserved.

This software is licensed under terms that can be found in the LICENSE file in the root directory of this software component. If no LICENSE file comes with this software, it is provided AS-\/\+IS. 

\label{doc-func-members}
\Hypertarget{stm32f4xx__hal__msp_8c_doc-func-members}
\doxysubsection{Function Documentation}
\Hypertarget{stm32f4xx__hal__msp_8c_a39b0f8e80268ab3e660ead921ad4b22f}\index{stm32f4xx\_hal\_msp.c@{stm32f4xx\_hal\_msp.c}!HAL\_ADC\_MspDeInit@{HAL\_ADC\_MspDeInit}}
\index{HAL\_ADC\_MspDeInit@{HAL\_ADC\_MspDeInit}!stm32f4xx\_hal\_msp.c@{stm32f4xx\_hal\_msp.c}}
\doxysubsubsection{\texorpdfstring{HAL\_ADC\_MspDeInit()}{HAL\_ADC\_MspDeInit()}}
{\footnotesize\ttfamily \label{stm32f4xx__hal__msp_8c_a39b0f8e80268ab3e660ead921ad4b22f} 
void HAL\+\_\+\+ADC\+\_\+\+Msp\+De\+Init (\begin{DoxyParamCaption}\item[{ADC\+\_\+\+Handle\+Type\+Def \texorpdfstring{$\ast$}{*}}]{hadc}{}\end{DoxyParamCaption})}

ADC MSP De-\/\+Initialization This function freeze the hardware resources used in this example. 

\begin{DoxyParams}{Parameters}
{\em hadc} & ADC handle pointer \\
\hline
\end{DoxyParams}

\begin{DoxyRetVals}{Return values}
{\em None} & \\
\hline
\end{DoxyRetVals}
ADC1 GPIO Configuration PB0 -\/-\/-\/-\/-\/-\/\texorpdfstring{$>$}{>} ADC1\+\_\+\+IN8\Hypertarget{stm32f4xx__hal__msp_8c_aa30863492d5c3103e3e8ce8a63dadd07}\index{stm32f4xx\_hal\_msp.c@{stm32f4xx\_hal\_msp.c}!HAL\_ADC\_MspInit@{HAL\_ADC\_MspInit}}
\index{HAL\_ADC\_MspInit@{HAL\_ADC\_MspInit}!stm32f4xx\_hal\_msp.c@{stm32f4xx\_hal\_msp.c}}
\doxysubsubsection{\texorpdfstring{HAL\_ADC\_MspInit()}{HAL\_ADC\_MspInit()}}
{\footnotesize\ttfamily \label{stm32f4xx__hal__msp_8c_aa30863492d5c3103e3e8ce8a63dadd07} 
void HAL\+\_\+\+ADC\+\_\+\+Msp\+Init (\begin{DoxyParamCaption}\item[{ADC\+\_\+\+Handle\+Type\+Def \texorpdfstring{$\ast$}{*}}]{hadc}{}\end{DoxyParamCaption})}

ADC MSP Initialization This function configures the hardware resources used in this example. 

\begin{DoxyParams}{Parameters}
{\em hadc} & ADC handle pointer \\
\hline
\end{DoxyParams}

\begin{DoxyRetVals}{Return values}
{\em None} & \\
\hline
\end{DoxyRetVals}
ADC1 GPIO Configuration PB0 -\/-\/-\/-\/-\/-\/\texorpdfstring{$>$}{>} ADC1\+\_\+\+IN8\Hypertarget{stm32f4xx__hal__msp_8c_a2ec8d9b09854c732e2feed549278f048}\index{stm32f4xx\_hal\_msp.c@{stm32f4xx\_hal\_msp.c}!HAL\_I2C\_MspDeInit@{HAL\_I2C\_MspDeInit}}
\index{HAL\_I2C\_MspDeInit@{HAL\_I2C\_MspDeInit}!stm32f4xx\_hal\_msp.c@{stm32f4xx\_hal\_msp.c}}
\doxysubsubsection{\texorpdfstring{HAL\_I2C\_MspDeInit()}{HAL\_I2C\_MspDeInit()}}
{\footnotesize\ttfamily \label{stm32f4xx__hal__msp_8c_a2ec8d9b09854c732e2feed549278f048} 
void HAL\+\_\+\+I2\+C\+\_\+\+Msp\+De\+Init (\begin{DoxyParamCaption}\item[{I2\+C\+\_\+\+Handle\+Type\+Def \texorpdfstring{$\ast$}{*}}]{hi2c}{}\end{DoxyParamCaption})}

I2C MSP De-\/\+Initialization This function freeze the hardware resources used in this example. 

\begin{DoxyParams}{Parameters}
{\em hi2c} & I2C handle pointer \\
\hline
\end{DoxyParams}

\begin{DoxyRetVals}{Return values}
{\em None} & \\
\hline
\end{DoxyRetVals}
I2\+C1 GPIO Configuration PB8 -\/-\/-\/-\/-\/-\/\texorpdfstring{$>$}{>} I2\+C1\+\_\+\+SCL PB9 -\/-\/-\/-\/-\/-\/\texorpdfstring{$>$}{>} I2\+C1\+\_\+\+SDA\Hypertarget{stm32f4xx__hal__msp_8c_abe01a202c27b23fc150aa66af3130073}\index{stm32f4xx\_hal\_msp.c@{stm32f4xx\_hal\_msp.c}!HAL\_I2C\_MspInit@{HAL\_I2C\_MspInit}}
\index{HAL\_I2C\_MspInit@{HAL\_I2C\_MspInit}!stm32f4xx\_hal\_msp.c@{stm32f4xx\_hal\_msp.c}}
\doxysubsubsection{\texorpdfstring{HAL\_I2C\_MspInit()}{HAL\_I2C\_MspInit()}}
{\footnotesize\ttfamily \label{stm32f4xx__hal__msp_8c_abe01a202c27b23fc150aa66af3130073} 
void HAL\+\_\+\+I2\+C\+\_\+\+Msp\+Init (\begin{DoxyParamCaption}\item[{I2\+C\+\_\+\+Handle\+Type\+Def \texorpdfstring{$\ast$}{*}}]{hi2c}{}\end{DoxyParamCaption})}

I2C MSP Initialization This function configures the hardware resources used in this example. 

\begin{DoxyParams}{Parameters}
{\em hi2c} & I2C handle pointer \\
\hline
\end{DoxyParams}

\begin{DoxyRetVals}{Return values}
{\em None} & \\
\hline
\end{DoxyRetVals}
I2\+C1 GPIO Configuration PB8 -\/-\/-\/-\/-\/-\/\texorpdfstring{$>$}{>} I2\+C1\+\_\+\+SCL PB9 -\/-\/-\/-\/-\/-\/\texorpdfstring{$>$}{>} I2\+C1\+\_\+\+SDA\Hypertarget{stm32f4xx__hal__msp_8c_ae4fb8e66865c87d0ebab74a726a6891f}\index{stm32f4xx\_hal\_msp.c@{stm32f4xx\_hal\_msp.c}!HAL\_MspInit@{HAL\_MspInit}}
\index{HAL\_MspInit@{HAL\_MspInit}!stm32f4xx\_hal\_msp.c@{stm32f4xx\_hal\_msp.c}}
\doxysubsubsection{\texorpdfstring{HAL\_MspInit()}{HAL\_MspInit()}}
{\footnotesize\ttfamily \label{stm32f4xx__hal__msp_8c_ae4fb8e66865c87d0ebab74a726a6891f} 
void HAL\+\_\+\+Msp\+Init (\begin{DoxyParamCaption}\item[{void}]{}{}\end{DoxyParamCaption})}

Initializes the Global MSP. \Hypertarget{stm32f4xx__hal__msp_8c_a555b8a2d3c7a07341f8cb1255318fa2b}\index{stm32f4xx\_hal\_msp.c@{stm32f4xx\_hal\_msp.c}!HAL\_TIM\_Base\_MspDeInit@{HAL\_TIM\_Base\_MspDeInit}}
\index{HAL\_TIM\_Base\_MspDeInit@{HAL\_TIM\_Base\_MspDeInit}!stm32f4xx\_hal\_msp.c@{stm32f4xx\_hal\_msp.c}}
\doxysubsubsection{\texorpdfstring{HAL\_TIM\_Base\_MspDeInit()}{HAL\_TIM\_Base\_MspDeInit()}}
{\footnotesize\ttfamily \label{stm32f4xx__hal__msp_8c_a555b8a2d3c7a07341f8cb1255318fa2b} 
void HAL\+\_\+\+TIM\+\_\+\+Base\+\_\+\+Msp\+De\+Init (\begin{DoxyParamCaption}\item[{TIM\+\_\+\+Handle\+Type\+Def \texorpdfstring{$\ast$}{*}}]{htim\+\_\+base}{}\end{DoxyParamCaption})}

TIM\+\_\+\+Base MSP De-\/\+Initialization This function freeze the hardware resources used in this example. 

\begin{DoxyParams}{Parameters}
{\em htim\+\_\+base} & TIM\+\_\+\+Base handle pointer \\
\hline
\end{DoxyParams}

\begin{DoxyRetVals}{Return values}
{\em None} & \\
\hline
\end{DoxyRetVals}
TIM2 GPIO Configuration PA5 -\/-\/-\/-\/-\/-\/\texorpdfstring{$>$}{>} TIM2\+\_\+\+CH1\Hypertarget{stm32f4xx__hal__msp_8c_abb25ade2f7e3f7aae167bd52270c2b86}\index{stm32f4xx\_hal\_msp.c@{stm32f4xx\_hal\_msp.c}!HAL\_TIM\_Base\_MspInit@{HAL\_TIM\_Base\_MspInit}}
\index{HAL\_TIM\_Base\_MspInit@{HAL\_TIM\_Base\_MspInit}!stm32f4xx\_hal\_msp.c@{stm32f4xx\_hal\_msp.c}}
\doxysubsubsection{\texorpdfstring{HAL\_TIM\_Base\_MspInit()}{HAL\_TIM\_Base\_MspInit()}}
{\footnotesize\ttfamily \label{stm32f4xx__hal__msp_8c_abb25ade2f7e3f7aae167bd52270c2b86} 
void HAL\+\_\+\+TIM\+\_\+\+Base\+\_\+\+Msp\+Init (\begin{DoxyParamCaption}\item[{TIM\+\_\+\+Handle\+Type\+Def \texorpdfstring{$\ast$}{*}}]{htim\+\_\+base}{}\end{DoxyParamCaption})}

TIM\+\_\+\+Base MSP Initialization This function configures the hardware resources used in this example. 

\begin{DoxyParams}{Parameters}
{\em htim\+\_\+base} & TIM\+\_\+\+Base handle pointer \\
\hline
\end{DoxyParams}

\begin{DoxyRetVals}{Return values}
{\em None} & \\
\hline
\end{DoxyRetVals}
TIM2 GPIO Configuration PA5 -\/-\/-\/-\/-\/-\/\texorpdfstring{$>$}{>} TIM2\+\_\+\+CH1\Hypertarget{stm32f4xx__hal__msp_8c_a9a53eee786f7e7e0217ce5b466c75f8a}\index{stm32f4xx\_hal\_msp.c@{stm32f4xx\_hal\_msp.c}!HAL\_TIM\_Encoder\_MspDeInit@{HAL\_TIM\_Encoder\_MspDeInit}}
\index{HAL\_TIM\_Encoder\_MspDeInit@{HAL\_TIM\_Encoder\_MspDeInit}!stm32f4xx\_hal\_msp.c@{stm32f4xx\_hal\_msp.c}}
\doxysubsubsection{\texorpdfstring{HAL\_TIM\_Encoder\_MspDeInit()}{HAL\_TIM\_Encoder\_MspDeInit()}}
{\footnotesize\ttfamily \label{stm32f4xx__hal__msp_8c_a9a53eee786f7e7e0217ce5b466c75f8a} 
void HAL\+\_\+\+TIM\+\_\+\+Encoder\+\_\+\+Msp\+De\+Init (\begin{DoxyParamCaption}\item[{TIM\+\_\+\+Handle\+Type\+Def \texorpdfstring{$\ast$}{*}}]{htim\+\_\+encoder}{}\end{DoxyParamCaption})}

TIM\+\_\+\+Encoder MSP De-\/\+Initialization This function freeze the hardware resources used in this example. 

\begin{DoxyParams}{Parameters}
{\em htim\+\_\+encoder} & TIM\+\_\+\+Encoder handle pointer \\
\hline
\end{DoxyParams}

\begin{DoxyRetVals}{Return values}
{\em None} & \\
\hline
\end{DoxyRetVals}
TIM3 GPIO Configuration PA6 -\/-\/-\/-\/-\/-\/\texorpdfstring{$>$}{>} TIM3\+\_\+\+CH1 PA7 -\/-\/-\/-\/-\/-\/\texorpdfstring{$>$}{>} TIM3\+\_\+\+CH2

TIM4 GPIO Configuration PB6 -\/-\/-\/-\/-\/-\/\texorpdfstring{$>$}{>} TIM4\+\_\+\+CH1 PB7 -\/-\/-\/-\/-\/-\/\texorpdfstring{$>$}{>} TIM4\+\_\+\+CH2\Hypertarget{stm32f4xx__hal__msp_8c_a8cc723aedb4c01bc57cbe38c21f0b0a3}\index{stm32f4xx\_hal\_msp.c@{stm32f4xx\_hal\_msp.c}!HAL\_TIM\_Encoder\_MspInit@{HAL\_TIM\_Encoder\_MspInit}}
\index{HAL\_TIM\_Encoder\_MspInit@{HAL\_TIM\_Encoder\_MspInit}!stm32f4xx\_hal\_msp.c@{stm32f4xx\_hal\_msp.c}}
\doxysubsubsection{\texorpdfstring{HAL\_TIM\_Encoder\_MspInit()}{HAL\_TIM\_Encoder\_MspInit()}}
{\footnotesize\ttfamily \label{stm32f4xx__hal__msp_8c_a8cc723aedb4c01bc57cbe38c21f0b0a3} 
void HAL\+\_\+\+TIM\+\_\+\+Encoder\+\_\+\+Msp\+Init (\begin{DoxyParamCaption}\item[{TIM\+\_\+\+Handle\+Type\+Def \texorpdfstring{$\ast$}{*}}]{htim\+\_\+encoder}{}\end{DoxyParamCaption})}

TIM\+\_\+\+Encoder MSP Initialization This function configures the hardware resources used in this example. 

\begin{DoxyParams}{Parameters}
{\em htim\+\_\+encoder} & TIM\+\_\+\+Encoder handle pointer \\
\hline
\end{DoxyParams}

\begin{DoxyRetVals}{Return values}
{\em None} & \\
\hline
\end{DoxyRetVals}
TIM3 GPIO Configuration PA6 -\/-\/-\/-\/-\/-\/\texorpdfstring{$>$}{>} TIM3\+\_\+\+CH1 PA7 -\/-\/-\/-\/-\/-\/\texorpdfstring{$>$}{>} TIM3\+\_\+\+CH2

TIM4 GPIO Configuration PB6 -\/-\/-\/-\/-\/-\/\texorpdfstring{$>$}{>} TIM4\+\_\+\+CH1 PB7 -\/-\/-\/-\/-\/-\/\texorpdfstring{$>$}{>} TIM4\+\_\+\+CH2\Hypertarget{stm32f4xx__hal__msp_8c_ae70bce6c39d0b570a7523b86738cec4b}\index{stm32f4xx\_hal\_msp.c@{stm32f4xx\_hal\_msp.c}!HAL\_TIM\_MspPostInit@{HAL\_TIM\_MspPostInit}}
\index{HAL\_TIM\_MspPostInit@{HAL\_TIM\_MspPostInit}!stm32f4xx\_hal\_msp.c@{stm32f4xx\_hal\_msp.c}}
\doxysubsubsection{\texorpdfstring{HAL\_TIM\_MspPostInit()}{HAL\_TIM\_MspPostInit()}}
{\footnotesize\ttfamily \label{stm32f4xx__hal__msp_8c_ae70bce6c39d0b570a7523b86738cec4b} 
void HAL\+\_\+\+TIM\+\_\+\+Msp\+Post\+Init (\begin{DoxyParamCaption}\item[{TIM\+\_\+\+Handle\+Type\+Def \texorpdfstring{$\ast$}{*}}]{htim}{}\end{DoxyParamCaption})}

TIM1 GPIO Configuration PA8 -\/-\/-\/-\/-\/-\/\texorpdfstring{$>$}{>} TIM1\+\_\+\+CH1 PA9 -\/-\/-\/-\/-\/-\/\texorpdfstring{$>$}{>} TIM1\+\_\+\+CH2

TIM5 GPIO Configuration PA0-\/\+WKUP -\/-\/-\/-\/-\/-\/\texorpdfstring{$>$}{>} TIM5\+\_\+\+CH1 PA1 -\/-\/-\/-\/-\/-\/\texorpdfstring{$>$}{>} TIM5\+\_\+\+CH2\Hypertarget{stm32f4xx__hal__msp_8c_af5f524564b3a99a9f87f45227309e866}\index{stm32f4xx\_hal\_msp.c@{stm32f4xx\_hal\_msp.c}!HAL\_TIM\_PWM\_MspDeInit@{HAL\_TIM\_PWM\_MspDeInit}}
\index{HAL\_TIM\_PWM\_MspDeInit@{HAL\_TIM\_PWM\_MspDeInit}!stm32f4xx\_hal\_msp.c@{stm32f4xx\_hal\_msp.c}}
\doxysubsubsection{\texorpdfstring{HAL\_TIM\_PWM\_MspDeInit()}{HAL\_TIM\_PWM\_MspDeInit()}}
{\footnotesize\ttfamily \label{stm32f4xx__hal__msp_8c_af5f524564b3a99a9f87f45227309e866} 
void HAL\+\_\+\+TIM\+\_\+\+PWM\+\_\+\+Msp\+De\+Init (\begin{DoxyParamCaption}\item[{TIM\+\_\+\+Handle\+Type\+Def \texorpdfstring{$\ast$}{*}}]{htim\+\_\+pwm}{}\end{DoxyParamCaption})}

TIM\+\_\+\+PWM MSP De-\/\+Initialization This function freeze the hardware resources used in this example. 

\begin{DoxyParams}{Parameters}
{\em htim\+\_\+pwm} & TIM\+\_\+\+PWM handle pointer \\
\hline
\end{DoxyParams}

\begin{DoxyRetVals}{Return values}
{\em None} & \\
\hline
\end{DoxyRetVals}
\Hypertarget{stm32f4xx__hal__msp_8c_a24d5b9c609d8b753d95508419f4c1901}\index{stm32f4xx\_hal\_msp.c@{stm32f4xx\_hal\_msp.c}!HAL\_TIM\_PWM\_MspInit@{HAL\_TIM\_PWM\_MspInit}}
\index{HAL\_TIM\_PWM\_MspInit@{HAL\_TIM\_PWM\_MspInit}!stm32f4xx\_hal\_msp.c@{stm32f4xx\_hal\_msp.c}}
\doxysubsubsection{\texorpdfstring{HAL\_TIM\_PWM\_MspInit()}{HAL\_TIM\_PWM\_MspInit()}}
{\footnotesize\ttfamily \label{stm32f4xx__hal__msp_8c_a24d5b9c609d8b753d95508419f4c1901} 
void HAL\+\_\+\+TIM\+\_\+\+PWM\+\_\+\+Msp\+Init (\begin{DoxyParamCaption}\item[{TIM\+\_\+\+Handle\+Type\+Def \texorpdfstring{$\ast$}{*}}]{htim\+\_\+pwm}{}\end{DoxyParamCaption})}

TIM\+\_\+\+PWM MSP Initialization This function configures the hardware resources used in this example. 

\begin{DoxyParams}{Parameters}
{\em htim\+\_\+pwm} & TIM\+\_\+\+PWM handle pointer \\
\hline
\end{DoxyParams}

\begin{DoxyRetVals}{Return values}
{\em None} & \\
\hline
\end{DoxyRetVals}
\Hypertarget{stm32f4xx__hal__msp_8c_a718f39804e3b910d738a0e1e46151188}\index{stm32f4xx\_hal\_msp.c@{stm32f4xx\_hal\_msp.c}!HAL\_UART\_MspDeInit@{HAL\_UART\_MspDeInit}}
\index{HAL\_UART\_MspDeInit@{HAL\_UART\_MspDeInit}!stm32f4xx\_hal\_msp.c@{stm32f4xx\_hal\_msp.c}}
\doxysubsubsection{\texorpdfstring{HAL\_UART\_MspDeInit()}{HAL\_UART\_MspDeInit()}}
{\footnotesize\ttfamily \label{stm32f4xx__hal__msp_8c_a718f39804e3b910d738a0e1e46151188} 
void HAL\+\_\+\+UART\+\_\+\+Msp\+De\+Init (\begin{DoxyParamCaption}\item[{UART\+\_\+\+Handle\+Type\+Def \texorpdfstring{$\ast$}{*}}]{huart}{}\end{DoxyParamCaption})}

UART MSP De-\/\+Initialization This function freeze the hardware resources used in this example. 

\begin{DoxyParams}{Parameters}
{\em huart} & UART handle pointer \\
\hline
\end{DoxyParams}

\begin{DoxyRetVals}{Return values}
{\em None} & \\
\hline
\end{DoxyRetVals}
USART2 GPIO Configuration PA2 -\/-\/-\/-\/-\/-\/\texorpdfstring{$>$}{>} USART2\+\_\+\+TX PA3 -\/-\/-\/-\/-\/-\/\texorpdfstring{$>$}{>} USART2\+\_\+\+RX

USART6 GPIO Configuration PA11 -\/-\/-\/-\/-\/-\/\texorpdfstring{$>$}{>} USART6\+\_\+\+TX PA12 -\/-\/-\/-\/-\/-\/\texorpdfstring{$>$}{>} USART6\+\_\+\+RX\Hypertarget{stm32f4xx__hal__msp_8c_a0e553b32211877322f949b14801bbfa7}\index{stm32f4xx\_hal\_msp.c@{stm32f4xx\_hal\_msp.c}!HAL\_UART\_MspInit@{HAL\_UART\_MspInit}}
\index{HAL\_UART\_MspInit@{HAL\_UART\_MspInit}!stm32f4xx\_hal\_msp.c@{stm32f4xx\_hal\_msp.c}}
\doxysubsubsection{\texorpdfstring{HAL\_UART\_MspInit()}{HAL\_UART\_MspInit()}}
{\footnotesize\ttfamily \label{stm32f4xx__hal__msp_8c_a0e553b32211877322f949b14801bbfa7} 
void HAL\+\_\+\+UART\+\_\+\+Msp\+Init (\begin{DoxyParamCaption}\item[{UART\+\_\+\+Handle\+Type\+Def \texorpdfstring{$\ast$}{*}}]{huart}{}\end{DoxyParamCaption})}

UART MSP Initialization This function configures the hardware resources used in this example. 

\begin{DoxyParams}{Parameters}
{\em huart} & UART handle pointer \\
\hline
\end{DoxyParams}

\begin{DoxyRetVals}{Return values}
{\em None} & \\
\hline
\end{DoxyRetVals}
USART2 GPIO Configuration PA2 -\/-\/-\/-\/-\/-\/\texorpdfstring{$>$}{>} USART2\+\_\+\+TX PA3 -\/-\/-\/-\/-\/-\/\texorpdfstring{$>$}{>} USART2\+\_\+\+RX

USART6 GPIO Configuration PA11 -\/-\/-\/-\/-\/-\/\texorpdfstring{$>$}{>} USART6\+\_\+\+TX PA12 -\/-\/-\/-\/-\/-\/\texorpdfstring{$>$}{>} USART6\+\_\+\+RX

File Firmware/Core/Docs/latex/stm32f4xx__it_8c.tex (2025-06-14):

\doxysection{Src/stm32f4xx\+\_\+it.c File Reference}
\hypertarget{stm32f4xx__it_8c}{}\label{stm32f4xx__it_8c}\index{Src/stm32f4xx\_it.c@{Src/stm32f4xx\_it.c}}

Interrupt Service Routines.  

{\ttfamily \#include "{}main.\+h"{}}\newline
{\ttfamily \#include "{}stm32f4xx\+\_\+it.\+h"{}}\newline
\doxysubsubsection*{Functions}
\begin{DoxyCompactItemize}
\item 
\Hypertarget{stm32f4xx__it_8c_a6ad7a5e3ee69cb6db6a6b9111ba898bc}\label{stm32f4xx__it_8c_a6ad7a5e3ee69cb6db6a6b9111ba898bc} 
void {\bfseries NMI\+\_\+\+Handler} (void)
\begin{DoxyCompactList}\small\item\em This function handles Non maskable interrupt. \end{DoxyCompactList}\item 
\Hypertarget{stm32f4xx__it_8c_a2bffc10d5bd4106753b7c30e86903bea}\label{stm32f4xx__it_8c_a2bffc10d5bd4106753b7c30e86903bea} 
void {\bfseries Hard\+Fault\+\_\+\+Handler} (void)
\begin{DoxyCompactList}\small\item\em This function handles Hard fault interrupt. \end{DoxyCompactList}\item 
\Hypertarget{stm32f4xx__it_8c_a3150f74512510287a942624aa9b44cc5}\label{stm32f4xx__it_8c_a3150f74512510287a942624aa9b44cc5} 
void {\bfseries Mem\+Manage\+\_\+\+Handler} (void)
\begin{DoxyCompactList}\small\item\em This function handles Memory management fault. \end{DoxyCompactList}\item 
\Hypertarget{stm32f4xx__it_8c_a850cefb17a977292ae5eb4cafa9976c3}\label{stm32f4xx__it_8c_a850cefb17a977292ae5eb4cafa9976c3} 
void {\bfseries Bus\+Fault\+\_\+\+Handler} (void)
\begin{DoxyCompactList}\small\item\em This function handles Pre-\/fetch fault, memory access fault. \end{DoxyCompactList}\item 
\Hypertarget{stm32f4xx__it_8c_a1d98923de2ed6b7309b66f9ba2971647}\label{stm32f4xx__it_8c_a1d98923de2ed6b7309b66f9ba2971647} 
void {\bfseries Usage\+Fault\+\_\+\+Handler} (void)
\begin{DoxyCompactList}\small\item\em This function handles Undefined instruction or illegal state. \end{DoxyCompactList}\item 
\Hypertarget{stm32f4xx__it_8c_a3e5ddb3df0d62f2dc357e64a3f04a6ce}\label{stm32f4xx__it_8c_a3e5ddb3df0d62f2dc357e64a3f04a6ce} 
void {\bfseries SVC\+\_\+\+Handler} (void)
\begin{DoxyCompactList}\small\item\em This function handles System service call via SWI instruction. \end{DoxyCompactList}\item 
\Hypertarget{stm32f4xx__it_8c_adbdfb05858cc36fc520974df37ec3cb0}\label{stm32f4xx__it_8c_adbdfb05858cc36fc520974df37ec3cb0} 
void {\bfseries Debug\+Mon\+\_\+\+Handler} (void)
\begin{DoxyCompactList}\small\item\em This function handles Debug monitor. \end{DoxyCompactList}\item 
\Hypertarget{stm32f4xx__it_8c_a6303e1f258cbdc1f970ce579cc015623}\label{stm32f4xx__it_8c_a6303e1f258cbdc1f970ce579cc015623} 
void {\bfseries Pend\+SV\+\_\+\+Handler} (void)
\begin{DoxyCompactList}\small\item\em This function handles Pendable request for system service. \end{DoxyCompactList}\item 
\Hypertarget{stm32f4xx__it_8c_ab5e09814056d617c521549e542639b7e}\label{stm32f4xx__it_8c_ab5e09814056d617c521549e542639b7e} 
void {\bfseries Sys\+Tick\+\_\+\+Handler} (void)
\begin{DoxyCompactList}\small\item\em This function handles System tick timer. \end{DoxyCompactList}\item 
\Hypertarget{stm32f4xx__it_8c_ac201b60d58b0eba2ce0b55710eb3c4d0}\label{stm32f4xx__it_8c_ac201b60d58b0eba2ce0b55710eb3c4d0} 
void {\bfseries DMA1\+\_\+\+Stream5\+\_\+\+IRQHandler} (void)
\begin{DoxyCompactList}\small\item\em This function handles DMA1 stream5 global interrupt. \end{DoxyCompactList}\item 
\Hypertarget{stm32f4xx__it_8c_a0ca6fd0e6f77921dd1123539857ba0a8}\label{stm32f4xx__it_8c_a0ca6fd0e6f77921dd1123539857ba0a8} 
void {\bfseries USART2\+\_\+\+IRQHandler} (void)
\begin{DoxyCompactList}\small\item\em This function handles USART2 global interrupt. \end{DoxyCompactList}\item 
\Hypertarget{stm32f4xx__it_8c_a738473a5b43f6c92b80ce1d3d6f77ed9}\label{stm32f4xx__it_8c_a738473a5b43f6c92b80ce1d3d6f77ed9} 
void {\bfseries EXTI15\+\_\+10\+\_\+\+IRQHandler} (void)
\begin{DoxyCompactList}\small\item\em This function handles EXTI line\mbox{[}15\+:10\mbox{]} interrupts. \end{DoxyCompactList}\item 
\Hypertarget{stm32f4xx__it_8c_a12c827857d907ad0cccd586fd934d446}\label{stm32f4xx__it_8c_a12c827857d907ad0cccd586fd934d446} 
void {\bfseries USART6\+\_\+\+IRQHandler} (void)
\begin{DoxyCompactList}\small\item\em This function handles USART6 global interrupt. \end{DoxyCompactList}\end{DoxyCompactItemize}
\doxysubsubsection*{Variables}
\begin{DoxyCompactItemize}
\item 
\Hypertarget{stm32f4xx__it_8c_a784aa25dc7e4580cfbf80658340f482c}\label{stm32f4xx__it_8c_a784aa25dc7e4580cfbf80658340f482c} 
DMA\+\_\+\+Handle\+Type\+Def {\bfseries hdma\+\_\+usart2\+\_\+rx}
\item 
\Hypertarget{stm32f4xx__it_8c_aa9479c261d65eecedd3d9582f7f0f89c}\label{stm32f4xx__it_8c_aa9479c261d65eecedd3d9582f7f0f89c} 
UART\+\_\+\+Handle\+Type\+Def {\bfseries huart2}
\item 
\Hypertarget{stm32f4xx__it_8c_a38905dda1d2fbff006c69db48eddba9d}\label{stm32f4xx__it_8c_a38905dda1d2fbff006c69db48eddba9d} 
UART\+\_\+\+Handle\+Type\+Def {\bfseries huart6}
\begin{DoxyCompactList}\small\item\em UART handle used for redirecting printf output. \end{DoxyCompactList}\end{DoxyCompactItemize}

\doxysubsection{Detailed Description}
Interrupt Service Routines. 

\begin{DoxyAttention}{Attention}

\end{DoxyAttention}
Copyright (c) 2025 STMicroelectronics. All rights reserved.

This software is licensed under terms that can be found in the LICENSE file in the root directory of this software component. If no LICENSE file comes with this software, it is provided AS-\/\+IS.

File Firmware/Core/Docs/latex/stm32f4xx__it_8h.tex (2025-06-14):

\doxysection{Inc/stm32f4xx\+\_\+it.h File Reference}
\hypertarget{stm32f4xx__it_8h}{}\label{stm32f4xx__it_8h}\index{Inc/stm32f4xx\_it.h@{Inc/stm32f4xx\_it.h}}

This file contains the headers of the interrupt handlers.  

\doxysubsubsection*{Functions}
\begin{DoxyCompactItemize}
\item 
\Hypertarget{stm32f4xx__it_8h_a6ad7a5e3ee69cb6db6a6b9111ba898bc}\label{stm32f4xx__it_8h_a6ad7a5e3ee69cb6db6a6b9111ba898bc} 
void {\bfseries NMI\+\_\+\+Handler} (void)
\begin{DoxyCompactList}\small\item\em This function handles Non maskable interrupt. \end{DoxyCompactList}\item 
\Hypertarget{stm32f4xx__it_8h_a2bffc10d5bd4106753b7c30e86903bea}\label{stm32f4xx__it_8h_a2bffc10d5bd4106753b7c30e86903bea} 
void {\bfseries Hard\+Fault\+\_\+\+Handler} (void)
\begin{DoxyCompactList}\small\item\em This function handles Hard fault interrupt. \end{DoxyCompactList}\item 
\Hypertarget{stm32f4xx__it_8h_a3150f74512510287a942624aa9b44cc5}\label{stm32f4xx__it_8h_a3150f74512510287a942624aa9b44cc5} 
void {\bfseries Mem\+Manage\+\_\+\+Handler} (void)
\begin{DoxyCompactList}\small\item\em This function handles Memory management fault. \end{DoxyCompactList}\item 
\Hypertarget{stm32f4xx__it_8h_a850cefb17a977292ae5eb4cafa9976c3}\label{stm32f4xx__it_8h_a850cefb17a977292ae5eb4cafa9976c3} 
void {\bfseries Bus\+Fault\+\_\+\+Handler} (void)
\begin{DoxyCompactList}\small\item\em This function handles Pre-\/fetch fault, memory access fault. \end{DoxyCompactList}\item 
\Hypertarget{stm32f4xx__it_8h_a1d98923de2ed6b7309b66f9ba2971647}\label{stm32f4xx__it_8h_a1d98923de2ed6b7309b66f9ba2971647} 
void {\bfseries Usage\+Fault\+\_\+\+Handler} (void)
\begin{DoxyCompactList}\small\item\em This function handles Undefined instruction or illegal state. \end{DoxyCompactList}\item 
\Hypertarget{stm32f4xx__it_8h_a3e5ddb3df0d62f2dc357e64a3f04a6ce}\label{stm32f4xx__it_8h_a3e5ddb3df0d62f2dc357e64a3f04a6ce} 
void {\bfseries SVC\+\_\+\+Handler} (void)
\begin{DoxyCompactList}\small\item\em This function handles System service call via SWI instruction. \end{DoxyCompactList}\item 
\Hypertarget{stm32f4xx__it_8h_adbdfb05858cc36fc520974df37ec3cb0}\label{stm32f4xx__it_8h_adbdfb05858cc36fc520974df37ec3cb0} 
void {\bfseries Debug\+Mon\+\_\+\+Handler} (void)
\begin{DoxyCompactList}\small\item\em This function handles Debug monitor. \end{DoxyCompactList}\item 
\Hypertarget{stm32f4xx__it_8h_a6303e1f258cbdc1f970ce579cc015623}\label{stm32f4xx__it_8h_a6303e1f258cbdc1f970ce579cc015623} 
void {\bfseries Pend\+SV\+\_\+\+Handler} (void)
\begin{DoxyCompactList}\small\item\em This function handles Pendable request for system service. \end{DoxyCompactList}\item 
\Hypertarget{stm32f4xx__it_8h_ab5e09814056d617c521549e542639b7e}\label{stm32f4xx__it_8h_ab5e09814056d617c521549e542639b7e} 
void {\bfseries Sys\+Tick\+\_\+\+Handler} (void)
\begin{DoxyCompactList}\small\item\em This function handles System tick timer. \end{DoxyCompactList}\item 
\Hypertarget{stm32f4xx__it_8h_ac201b60d58b0eba2ce0b55710eb3c4d0}\label{stm32f4xx__it_8h_ac201b60d58b0eba2ce0b55710eb3c4d0} 
void {\bfseries DMA1\+\_\+\+Stream5\+\_\+\+IRQHandler} (void)
\begin{DoxyCompactList}\small\item\em This function handles DMA1 stream5 global interrupt. \end{DoxyCompactList}\item 
\Hypertarget{stm32f4xx__it_8h_a0ca6fd0e6f77921dd1123539857ba0a8}\label{stm32f4xx__it_8h_a0ca6fd0e6f77921dd1123539857ba0a8} 
void {\bfseries USART2\+\_\+\+IRQHandler} (void)
\begin{DoxyCompactList}\small\item\em This function handles USART2 global interrupt. \end{DoxyCompactList}\item 
\Hypertarget{stm32f4xx__it_8h_a738473a5b43f6c92b80ce1d3d6f77ed9}\label{stm32f4xx__it_8h_a738473a5b43f6c92b80ce1d3d6f77ed9} 
void {\bfseries EXTI15\+\_\+10\+\_\+\+IRQHandler} (void)
\begin{DoxyCompactList}\small\item\em This function handles EXTI line\mbox{[}15\+:10\mbox{]} interrupts. \end{DoxyCompactList}\item 
\Hypertarget{stm32f4xx__it_8h_a12c827857d907ad0cccd586fd934d446}\label{stm32f4xx__it_8h_a12c827857d907ad0cccd586fd934d446} 
void {\bfseries USART6\+\_\+\+IRQHandler} (void)
\begin{DoxyCompactList}\small\item\em This function handles USART6 global interrupt. \end{DoxyCompactList}\end{DoxyCompactItemize}

\doxysubsection{Detailed Description}
This file contains the headers of the interrupt handlers. 

\begin{DoxyAttention}{Attention}

\end{DoxyAttention}
Copyright (c) 2025 STMicroelectronics. All rights reserved.

This software is licensed under terms that can be found in the LICENSE file in the root directory of this software component. If no LICENSE file comes with this software, it is provided AS-\/\+IS.

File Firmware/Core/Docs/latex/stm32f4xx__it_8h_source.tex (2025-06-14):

\doxysection{stm32f4xx\+\_\+it.\+h}
\hypertarget{stm32f4xx__it_8h_source}{}\label{stm32f4xx__it_8h_source}\index{Inc/stm32f4xx\_it.h@{Inc/stm32f4xx\_it.h}}
\mbox{\hyperlink{stm32f4xx__it_8h}{Go to the documentation of this file.}}
\begin{DoxyCode}{0}
\DoxyCodeLine{00001\ \textcolor{comment}{/*\ USER\ CODE\ BEGIN\ Header\ */}}
\DoxyCodeLine{00018\ \textcolor{comment}{/*\ USER\ CODE\ END\ Header\ */}}
\DoxyCodeLine{00019\ }
\DoxyCodeLine{00020\ \textcolor{comment}{/*\ Define\ to\ prevent\ recursive\ inclusion\ -\/-\/-\/-\/-\/-\/-\/-\/-\/-\/-\/-\/-\/-\/-\/-\/-\/-\/-\/-\/-\/-\/-\/-\/-\/-\/-\/-\/-\/-\/-\/-\/-\/-\/-\/-\/-\/*/}}
\DoxyCodeLine{00021\ \textcolor{preprocessor}{\#ifndef\ \_\_STM32F4xx\_IT\_H}}
\DoxyCodeLine{00022\ \textcolor{preprocessor}{\#define\ \_\_STM32F4xx\_IT\_H}}
\DoxyCodeLine{00023\ }
\DoxyCodeLine{00024\ \textcolor{preprocessor}{\#ifdef\ \_\_cplusplus}}
\DoxyCodeLine{00025\ \textcolor{keyword}{extern}\ \textcolor{stringliteral}{"{}C"{}}\ \{}
\DoxyCodeLine{00026\ \textcolor{preprocessor}{\#endif}}
\DoxyCodeLine{00027\ }
\DoxyCodeLine{00028\ \textcolor{comment}{/*\ Private\ includes\ -\/-\/-\/-\/-\/-\/-\/-\/-\/-\/-\/-\/-\/-\/-\/-\/-\/-\/-\/-\/-\/-\/-\/-\/-\/-\/-\/-\/-\/-\/-\/-\/-\/-\/-\/-\/-\/-\/-\/-\/-\/-\/-\/-\/-\/-\/-\/-\/-\/-\/-\/-\/-\/-\/-\/-\/-\/-\/*/}}
\DoxyCodeLine{00029\ \textcolor{comment}{/*\ USER\ CODE\ BEGIN\ Includes\ */}}
\DoxyCodeLine{00030\ }
\DoxyCodeLine{00031\ \textcolor{comment}{/*\ USER\ CODE\ END\ Includes\ */}}
\DoxyCodeLine{00032\ }
\DoxyCodeLine{00033\ \textcolor{comment}{/*\ Exported\ types\ -\/-\/-\/-\/-\/-\/-\/-\/-\/-\/-\/-\/-\/-\/-\/-\/-\/-\/-\/-\/-\/-\/-\/-\/-\/-\/-\/-\/-\/-\/-\/-\/-\/-\/-\/-\/-\/-\/-\/-\/-\/-\/-\/-\/-\/-\/-\/-\/-\/-\/-\/-\/-\/-\/-\/-\/-\/-\/-\/-\/*/}}
\DoxyCodeLine{00034\ \textcolor{comment}{/*\ USER\ CODE\ BEGIN\ ET\ */}}
\DoxyCodeLine{00035\ }
\DoxyCodeLine{00036\ \textcolor{comment}{/*\ USER\ CODE\ END\ ET\ */}}
\DoxyCodeLine{00037\ }
\DoxyCodeLine{00038\ \textcolor{comment}{/*\ Exported\ constants\ -\/-\/-\/-\/-\/-\/-\/-\/-\/-\/-\/-\/-\/-\/-\/-\/-\/-\/-\/-\/-\/-\/-\/-\/-\/-\/-\/-\/-\/-\/-\/-\/-\/-\/-\/-\/-\/-\/-\/-\/-\/-\/-\/-\/-\/-\/-\/-\/-\/-\/-\/-\/-\/-\/-\/-\/*/}}
\DoxyCodeLine{00039\ \textcolor{comment}{/*\ USER\ CODE\ BEGIN\ EC\ */}}
\DoxyCodeLine{00040\ }
\DoxyCodeLine{00041\ \textcolor{comment}{/*\ USER\ CODE\ END\ EC\ */}}
\DoxyCodeLine{00042\ }
\DoxyCodeLine{00043\ \textcolor{comment}{/*\ Exported\ macro\ -\/-\/-\/-\/-\/-\/-\/-\/-\/-\/-\/-\/-\/-\/-\/-\/-\/-\/-\/-\/-\/-\/-\/-\/-\/-\/-\/-\/-\/-\/-\/-\/-\/-\/-\/-\/-\/-\/-\/-\/-\/-\/-\/-\/-\/-\/-\/-\/-\/-\/-\/-\/-\/-\/-\/-\/-\/-\/-\/-\/*/}}
\DoxyCodeLine{00044\ \textcolor{comment}{/*\ USER\ CODE\ BEGIN\ EM\ */}}
\DoxyCodeLine{00045\ }
\DoxyCodeLine{00046\ \textcolor{comment}{/*\ USER\ CODE\ END\ EM\ */}}
\DoxyCodeLine{00047\ }
\DoxyCodeLine{00048\ \textcolor{comment}{/*\ Exported\ functions\ prototypes\ -\/-\/-\/-\/-\/-\/-\/-\/-\/-\/-\/-\/-\/-\/-\/-\/-\/-\/-\/-\/-\/-\/-\/-\/-\/-\/-\/-\/-\/-\/-\/-\/-\/-\/-\/-\/-\/-\/-\/-\/-\/-\/-\/-\/-\/*/}}
\DoxyCodeLine{00049\ \textcolor{keywordtype}{void}\ \mbox{\hyperlink{stm32f4xx__it_8h_a6ad7a5e3ee69cb6db6a6b9111ba898bc}{NMI\_Handler}}(\textcolor{keywordtype}{void});}
\DoxyCodeLine{00050\ \textcolor{keywordtype}{void}\ \mbox{\hyperlink{stm32f4xx__it_8h_a2bffc10d5bd4106753b7c30e86903bea}{HardFault\_Handler}}(\textcolor{keywordtype}{void});}
\DoxyCodeLine{00051\ \textcolor{keywordtype}{void}\ \mbox{\hyperlink{stm32f4xx__it_8h_a3150f74512510287a942624aa9b44cc5}{MemManage\_Handler}}(\textcolor{keywordtype}{void});}
\DoxyCodeLine{00052\ \textcolor{keywordtype}{void}\ \mbox{\hyperlink{stm32f4xx__it_8h_a850cefb17a977292ae5eb4cafa9976c3}{BusFault\_Handler}}(\textcolor{keywordtype}{void});}
\DoxyCodeLine{00053\ \textcolor{keywordtype}{void}\ \mbox{\hyperlink{stm32f4xx__it_8h_a1d98923de2ed6b7309b66f9ba2971647}{UsageFault\_Handler}}(\textcolor{keywordtype}{void});}
\DoxyCodeLine{00054\ \textcolor{keywordtype}{void}\ \mbox{\hyperlink{stm32f4xx__it_8h_a3e5ddb3df0d62f2dc357e64a3f04a6ce}{SVC\_Handler}}(\textcolor{keywordtype}{void});}
\DoxyCodeLine{00055\ \textcolor{keywordtype}{void}\ \mbox{\hyperlink{stm32f4xx__it_8h_adbdfb05858cc36fc520974df37ec3cb0}{DebugMon\_Handler}}(\textcolor{keywordtype}{void});}
\DoxyCodeLine{00056\ \textcolor{keywordtype}{void}\ \mbox{\hyperlink{stm32f4xx__it_8h_a6303e1f258cbdc1f970ce579cc015623}{PendSV\_Handler}}(\textcolor{keywordtype}{void});}
\DoxyCodeLine{00057\ \textcolor{keywordtype}{void}\ \mbox{\hyperlink{stm32f4xx__it_8h_ab5e09814056d617c521549e542639b7e}{SysTick\_Handler}}(\textcolor{keywordtype}{void});}
\DoxyCodeLine{00058\ \textcolor{keywordtype}{void}\ \mbox{\hyperlink{stm32f4xx__it_8h_ac201b60d58b0eba2ce0b55710eb3c4d0}{DMA1\_Stream5\_IRQHandler}}(\textcolor{keywordtype}{void});}
\DoxyCodeLine{00059\ \textcolor{keywordtype}{void}\ \mbox{\hyperlink{stm32f4xx__it_8h_a0ca6fd0e6f77921dd1123539857ba0a8}{USART2\_IRQHandler}}(\textcolor{keywordtype}{void});}
\DoxyCodeLine{00060\ \textcolor{keywordtype}{void}\ \mbox{\hyperlink{stm32f4xx__it_8h_a738473a5b43f6c92b80ce1d3d6f77ed9}{EXTI15\_10\_IRQHandler}}(\textcolor{keywordtype}{void});}
\DoxyCodeLine{00061\ \textcolor{keywordtype}{void}\ \mbox{\hyperlink{stm32f4xx__it_8h_a12c827857d907ad0cccd586fd934d446}{USART6\_IRQHandler}}(\textcolor{keywordtype}{void});}
\DoxyCodeLine{00062\ \textcolor{comment}{/*\ USER\ CODE\ BEGIN\ EFP\ */}}
\DoxyCodeLine{00063\ }
\DoxyCodeLine{00064\ \textcolor{comment}{/*\ USER\ CODE\ END\ EFP\ */}}
\DoxyCodeLine{00065\ }
\DoxyCodeLine{00066\ \textcolor{preprocessor}{\#ifdef\ \_\_cplusplus}}
\DoxyCodeLine{00067\ \}}
\DoxyCodeLine{00068\ \textcolor{preprocessor}{\#endif}}
\DoxyCodeLine{00069\ }
\DoxyCodeLine{00070\ \textcolor{preprocessor}{\#endif\ }\textcolor{comment}{/*\ \_\_STM32F4xx\_IT\_H\ */}\textcolor{preprocessor}{}}

\end{DoxyCode}

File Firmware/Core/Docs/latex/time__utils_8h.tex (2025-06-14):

\doxysection{Inc/time\+\_\+utils.h File Reference}
\hypertarget{time__utils_8h}{}\label{time__utils_8h}\index{Inc/time\_utils.h@{Inc/time\_utils.h}}

Utility functions for microsecond-\/level timing.  

{\ttfamily \#include $<$stm32f4xx\+\_\+hal.\+h$>$}\newline
{\ttfamily \#include $<$stdint.\+h$>$}\newline
\doxysubsubsection*{Functions}
\begin{DoxyCompactItemize}
\item 
uint32\+\_\+t \mbox{\hyperlink{time__utils_8h_af543edc4b91ee97e556de2f0bbc709ad}{micros}} (void)
\begin{DoxyCompactList}\small\item\em Returns the number of microseconds since the timer started. \end{DoxyCompactList}\item 
void \mbox{\hyperlink{time__utils_8h_ab33ebb2c5ca2d80d259c64a9d658589f}{delay\+\_\+us}} (uint32\+\_\+t us)
\begin{DoxyCompactList}\small\item\em Delays execution for a specified number of microseconds. \end{DoxyCompactList}\end{DoxyCompactItemize}

\doxysubsection{Detailed Description}
Utility functions for microsecond-\/level timing. 

Provides lightweight timing utilities based on hardware timers, useful for precise control loop execution and delay functions. 

\label{doc-func-members}
\Hypertarget{time__utils_8h_doc-func-members}
\doxysubsection{Function Documentation}
\Hypertarget{time__utils_8h_ab33ebb2c5ca2d80d259c64a9d658589f}\index{time\_utils.h@{time\_utils.h}!delay\_us@{delay\_us}}
\index{delay\_us@{delay\_us}!time\_utils.h@{time\_utils.h}}
\doxysubsubsection{\texorpdfstring{delay\_us()}{delay\_us()}}
{\footnotesize\ttfamily \label{time__utils_8h_ab33ebb2c5ca2d80d259c64a9d658589f} 
void delay\+\_\+us (\begin{DoxyParamCaption}\item[{uint32\+\_\+t}]{us}{}\end{DoxyParamCaption})}

Delays execution for a specified number of microseconds. 

\begin{DoxyParams}{Parameters}
{\em us} & Delay duration in microseconds. \\
\hline
\end{DoxyParams}
\begin{DoxyNote}{Note}
Busy-\/wait implementation; not RTOS-\/friendly.
\end{DoxyNote}
Delays execution for a specified number of microseconds.

\begin{DoxyParams}{Parameters}
{\em us} & Number of microseconds to delay.\\
\hline
\end{DoxyParams}
Uses a busy-\/wait loop based on the {\ttfamily \doxylink{time__utils_8h_af543edc4b91ee97e556de2f0bbc709ad}{micros()}} counter. \begin{DoxyNote}{Note}
Not suitable for power-\/sensitive applications or inside ISRs. 
\end{DoxyNote}
\Hypertarget{time__utils_8h_af543edc4b91ee97e556de2f0bbc709ad}\index{time\_utils.h@{time\_utils.h}!micros@{micros}}
\index{micros@{micros}!time\_utils.h@{time\_utils.h}}
\doxysubsubsection{\texorpdfstring{micros()}{micros()}}
{\footnotesize\ttfamily \label{time__utils_8h_af543edc4b91ee97e556de2f0bbc709ad} 
uint32\+\_\+t micros (\begin{DoxyParamCaption}\item[{void}]{}{}\end{DoxyParamCaption})}

Returns the number of microseconds since the timer started. 

\begin{DoxyReturn}{Returns}
Elapsed time in microseconds as a 32-\/bit unsigned integer. 
\end{DoxyReturn}
\begin{DoxyNote}{Note}
Requires a configured timer (e.\+g., TIM2) running at 1 MHz.
\end{DoxyNote}
Returns the number of microseconds since the timer started.

Reads the current counter value from the TIM2 peripheral. \begin{DoxyReturn}{Returns}
Current microsecond timestamp as a 32-\/bit unsigned integer. 
\end{DoxyReturn}

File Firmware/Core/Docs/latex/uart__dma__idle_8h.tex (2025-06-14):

\doxysection{Inc/uart\+\_\+dma\+\_\+idle.h File Reference}
\hypertarget{uart__dma__idle_8h}{}\label{uart__dma__idle_8h}\index{Inc/uart\_dma\_idle.h@{Inc/uart\_dma\_idle.h}}

UART DMA with idle line detection handler.  

{\ttfamily \#include "{}stm32f4xx\+\_\+hal.\+h"{}}\newline
\doxysubsubsection*{Macros}
\begin{DoxyCompactItemize}
\item 
\Hypertarget{uart__dma__idle_8h_a6b20d41d6252e9871430c242cb1a56e7}\label{uart__dma__idle_8h_a6b20d41d6252e9871430c242cb1a56e7} 
\#define {\bfseries BUFFER\+\_\+\+SIZE}~64
\begin{DoxyCompactList}\small\item\em Maximum receive buffer size for UART DMA. \end{DoxyCompactList}\end{DoxyCompactItemize}
\doxysubsubsection*{Functions}
\begin{DoxyCompactItemize}
\item 
void \mbox{\hyperlink{uart__dma__idle_8h_a05a9aa3c7d6d9c513316cb3bc246c6db}{UART\+\_\+\+DMA\+\_\+\+IDLE\+\_\+\+Init}} (UART\+\_\+\+Handle\+Type\+Def \texorpdfstring{$\ast$}{*}huart)
\begin{DoxyCompactList}\small\item\em Initializes UART DMA reception with idle line detection. \end{DoxyCompactList}\item 
void \mbox{\hyperlink{uart__dma__idle_8h_a9473c823f41276615e26ed3741652dc7}{UART\+\_\+\+DMA\+\_\+\+IDLE\+\_\+\+IRQHandler}} (UART\+\_\+\+Handle\+Type\+Def \texorpdfstring{$\ast$}{*}huart)
\begin{DoxyCompactList}\small\item\em UART interrupt handler for idle line detection. \end{DoxyCompactList}\end{DoxyCompactItemize}
\doxysubsubsection*{Variables}
\begin{DoxyCompactItemize}
\item 
uint8\+\_\+t \mbox{\hyperlink{uart__dma__idle_8h_a7859af7e1d2d58c1bc67f781bbfbe818}{rx\+\_\+buffer}} \mbox{[}\mbox{\hyperlink{command__parser_8h_a6b20d41d6252e9871430c242cb1a56e7}{BUFFER\+\_\+\+SIZE}}\mbox{]}
\begin{DoxyCompactList}\small\item\em UART DMA receive buffer shared with command parser or control logic. \end{DoxyCompactList}\item 
uint8\+\_\+t \mbox{\hyperlink{uart__dma__idle_8h_a2359bfa4a10109d5dcc2e002cb8ece47}{buffer\+\_\+index}}
\begin{DoxyCompactList}\small\item\em Current write index into the rx\+\_\+buffer. \end{DoxyCompactList}\item 
volatile uint8\+\_\+t \mbox{\hyperlink{uart__dma__idle_8h_a6dcf3de33714573b301e5db87df1f4f9}{command\+\_\+ready}}
\begin{DoxyCompactList}\small\item\em Flag set when a full command is received and ready to parse. \end{DoxyCompactList}\end{DoxyCompactItemize}

\doxysubsection{Detailed Description}
UART DMA with idle line detection handler. 

Provides support for non-\/blocking UART reception using DMA with idle line interrupt to detect end-\/of-\/packet or message termination. 

\label{doc-func-members}
\Hypertarget{uart__dma__idle_8h_doc-func-members}
\doxysubsection{Function Documentation}
\Hypertarget{uart__dma__idle_8h_a05a9aa3c7d6d9c513316cb3bc246c6db}\index{uart\_dma\_idle.h@{uart\_dma\_idle.h}!UART\_DMA\_IDLE\_Init@{UART\_DMA\_IDLE\_Init}}
\index{UART\_DMA\_IDLE\_Init@{UART\_DMA\_IDLE\_Init}!uart\_dma\_idle.h@{uart\_dma\_idle.h}}
\doxysubsubsection{\texorpdfstring{UART\_DMA\_IDLE\_Init()}{UART\_DMA\_IDLE\_Init()}}
{\footnotesize\ttfamily \label{uart__dma__idle_8h_a05a9aa3c7d6d9c513316cb3bc246c6db} 
void UART\+\_\+\+DMA\+\_\+\+IDLE\+\_\+\+Init (\begin{DoxyParamCaption}\item[{UART\+\_\+\+Handle\+Type\+Def \texorpdfstring{$\ast$}{*}}]{huart}{}\end{DoxyParamCaption})}

Initializes UART DMA reception with idle line detection. 

\begin{DoxyParams}{Parameters}
{\em huart} & Pointer to UART handle configured for DMA RX.\\
\hline
\end{DoxyParams}
Initializes UART DMA reception with idle line detection.

\begin{DoxyParams}{Parameters}
{\em huart} & Pointer to the UART handle to configure.\\
\hline
\end{DoxyParams}
Starts the DMA reception and enables UART idle line detection to trigger when a message has ended. Assumes a \textquotesingle{}\textbackslash{}r~\newline
\textquotesingle{} terminated protocol. \Hypertarget{uart__dma__idle_8h_a9473c823f41276615e26ed3741652dc7}\index{uart\_dma\_idle.h@{uart\_dma\_idle.h}!UART\_DMA\_IDLE\_IRQHandler@{UART\_DMA\_IDLE\_IRQHandler}}
\index{UART\_DMA\_IDLE\_IRQHandler@{UART\_DMA\_IDLE\_IRQHandler}!uart\_dma\_idle.h@{uart\_dma\_idle.h}}
\doxysubsubsection{\texorpdfstring{UART\_DMA\_IDLE\_IRQHandler()}{UART\_DMA\_IDLE\_IRQHandler()}}
{\footnotesize\ttfamily \label{uart__dma__idle_8h_a9473c823f41276615e26ed3741652dc7} 
void UART\+\_\+\+DMA\+\_\+\+IDLE\+\_\+\+IRQHandler (\begin{DoxyParamCaption}\item[{UART\+\_\+\+Handle\+Type\+Def \texorpdfstring{$\ast$}{*}}]{huart}{}\end{DoxyParamCaption})}

UART interrupt handler for idle line detection. 

\begin{DoxyParams}{Parameters}
{\em huart} & Pointer to UART handle triggering the interrupt.\\
\hline
\end{DoxyParams}
Should be called from the HAL\+\_\+\+UART\+\_\+\+IRQHandler.

UART interrupt handler for idle line detection.

\begin{DoxyParams}{Parameters}
{\em huart} & Pointer to the UART handle triggering the interrupt.\\
\hline
\end{DoxyParams}
Stops DMA temporarily, calculates received length, and checks for a complete command (terminated by "{}\textbackslash{}r\textbackslash{}n"{}). If found, sets {\ttfamily command\+\_\+ready}.
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

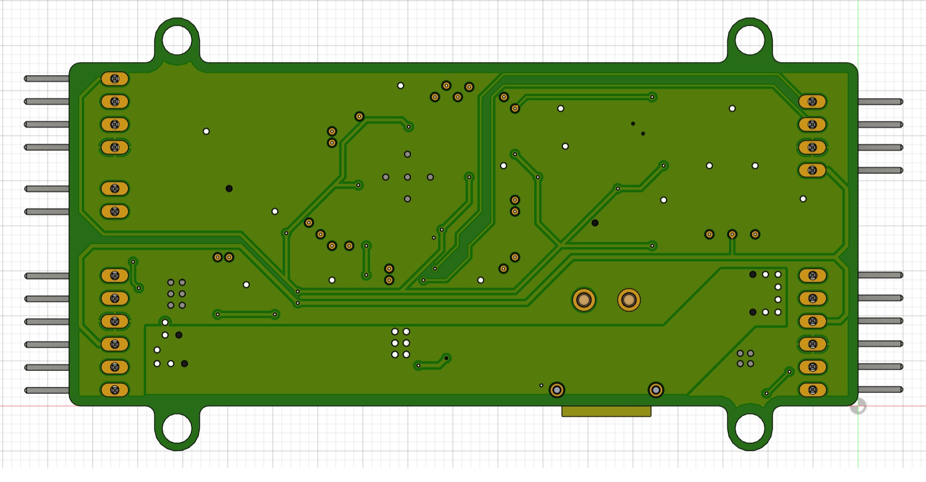
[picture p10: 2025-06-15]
Hardware/Electrical/PCB_Back.jpg

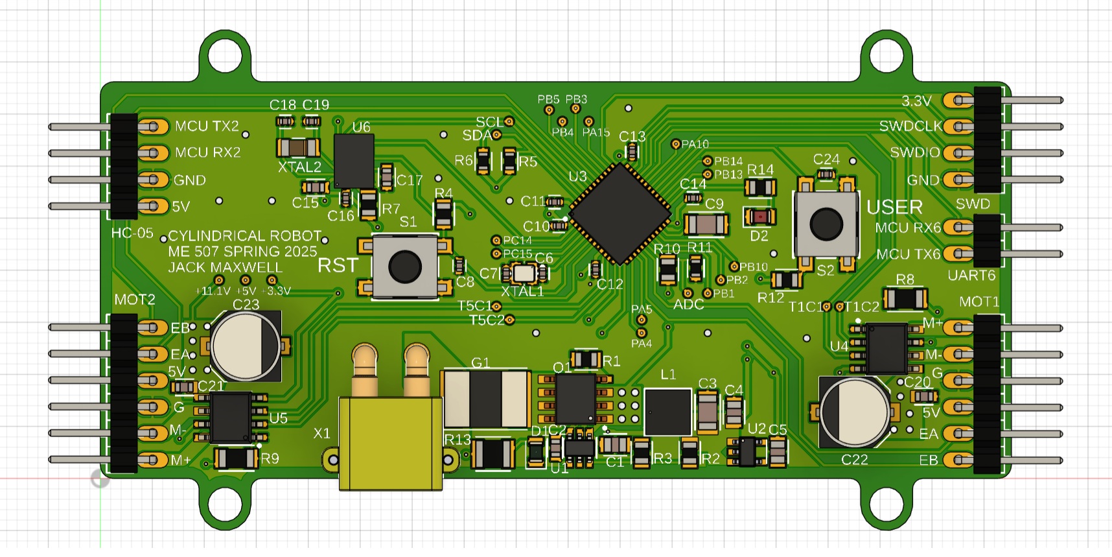
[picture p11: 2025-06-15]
Hardware/Electrical/PCB_Front.jpg

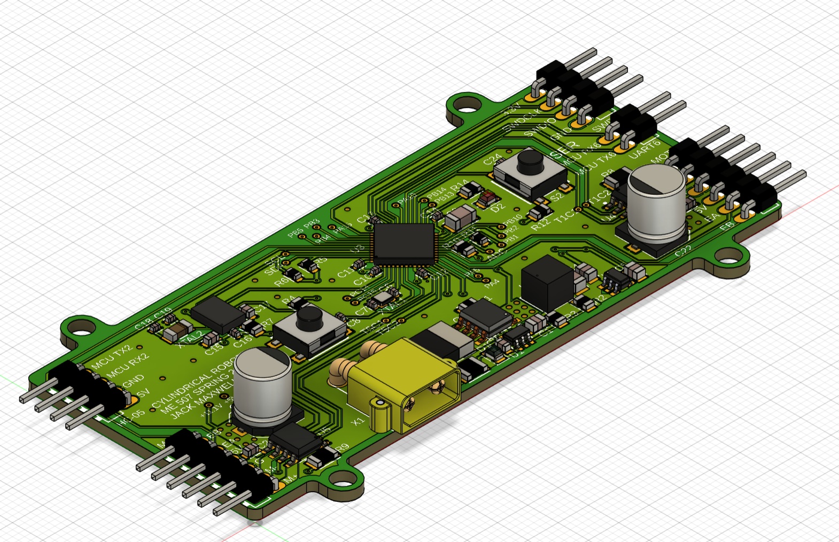
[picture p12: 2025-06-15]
Hardware/Electrical/PCB_Isometric.jpg

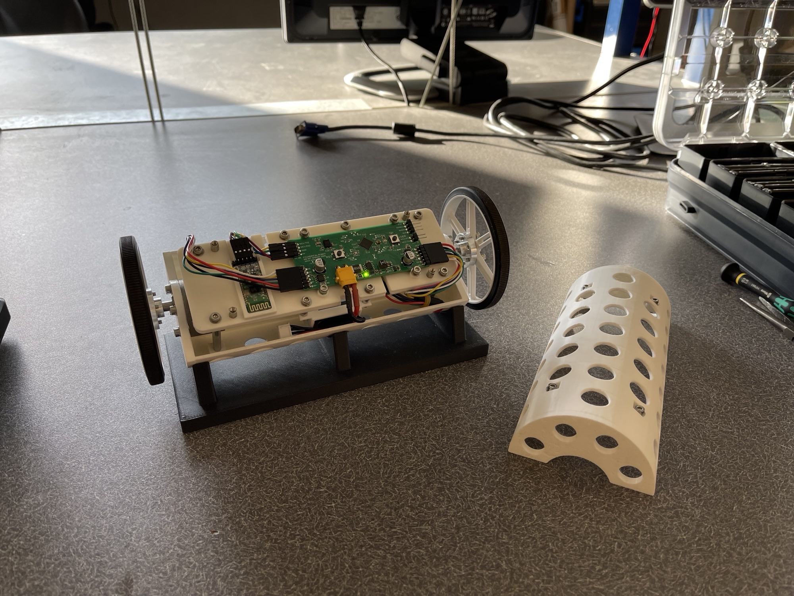
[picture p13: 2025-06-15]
Hardware/Mechanical/Robot_Open.jpg

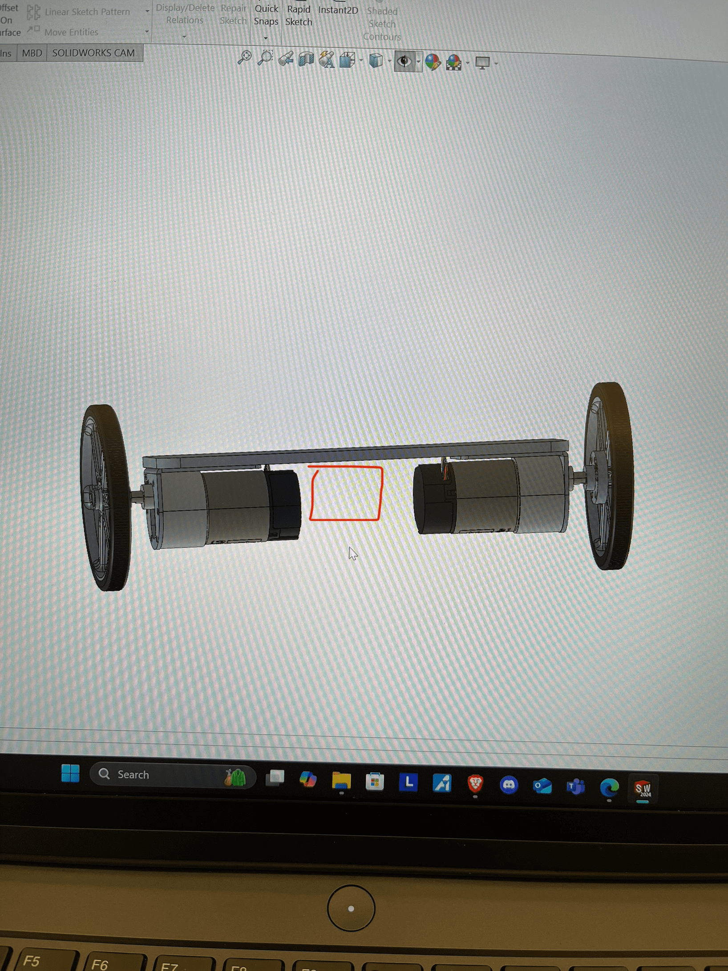
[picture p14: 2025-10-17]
Media/Preliminary_Robot_CAD_2.png

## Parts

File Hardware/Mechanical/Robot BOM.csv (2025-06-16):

Item | Manufacturer | Part # | Quantity | Link
Wheels | Pololu | 1439 | 1 | https://www.pololu.com/product/1439
Mounting Hub | Pololu | 1999 | 1 | https://www.pololu.com/product/1999
DC Gearmotors | Pololu | 4751 | 2 | https://www.pololu.com/product/4751
M-F Standoffs | McMaster-Carr | 98952A108 | 4 | https://www.mcmaster.com/98952A108/
Long F-F Standoffs | McMaster-Carr | 95947A020 | 4 | https://www.mcmaster.com/95947A020/
Short F-F Standoffs | McMaster-Carr | 94868A162 | 4 | https://www.mcmaster.com/94868A162/

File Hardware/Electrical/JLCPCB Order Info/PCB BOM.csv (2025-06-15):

Comment | Designator | Footprint | JLCPCB Part #
25MHz Crystal | XTAL1 | SMD2016-4P | C19711739
32.768kHz Crystal | XTAL2 | SMD3215-2P | C156244
Tactile Switch | S1, S2 | SMD 6x6mm 3.5mm | C5183855
8A Trip Fuse | G1 | 2920 | C720182
30V 10A PMOSFET | Q1 | SOIC-8 | C3000
600mA Step-Down Regulator | U1 | SOT-23-6 | C3193129
300mA LDO Regulator | U2 | SOT-23-5 | C2862740
STM32F411CEU6 MCU | U3 | UFQFPN-48(7x7) | C60420
Brushed DC Motor Driver | U4, U5 | SOPowerPAD(DDA)-8 | C5218850
BNO055 IMU | U6 | LGA-28(3.8x5.2) | C93216
10kΩ | R1, R4, R7, R10, R12 | 0805 | C84376
118kΩ | R2 | 0805 | C103948
22.1kΩ | R3 | 0805 | C204311
2.2kΩ | R5, R6 | 0603 | C114662
100mΩ, 0.5W | R8, R9 | 1206 | C346763
3.6kΩ | R11 | 0603 | C137729
560Ω, 0.5W | R13 | 1210 | C3000758
270Ω, .125W | R14 | 0805 | C485675
2.2uF, 25V, X7R | C1 | 0805 | C19110
.1uF, 16V, X7R | C2 | 0603 | C66501
22uF, 10V, X7R | C3 | 1206 | C909845
1uF, 10V, X7R | C4, C5, C17 | 0805 | C1712
2pF, 10V, X8R | C6, C7, C18, C19 | 0402 | C161316
100nF, 10V, X7R | C8, C10-14, C16, C24 | 0402 | C1525
4.7uF, 10V, X7R | C9 | 1206 | C1872
120nF, 10V, X7R | C15 | 0603 | C107063
100nF, 25V, X7R | C20, C21 | 0603 | C1590
330uF, 25V, AEC-Q200 | C22, C23 | SMD,D6.3xL7.7mm | C2980171
15uH | L1 | 1616 | C3911667
20mA 2.1V Green | D1 | 0805 | C5875740
5mA 2.0V Red | D2 | 0805 | C5349939

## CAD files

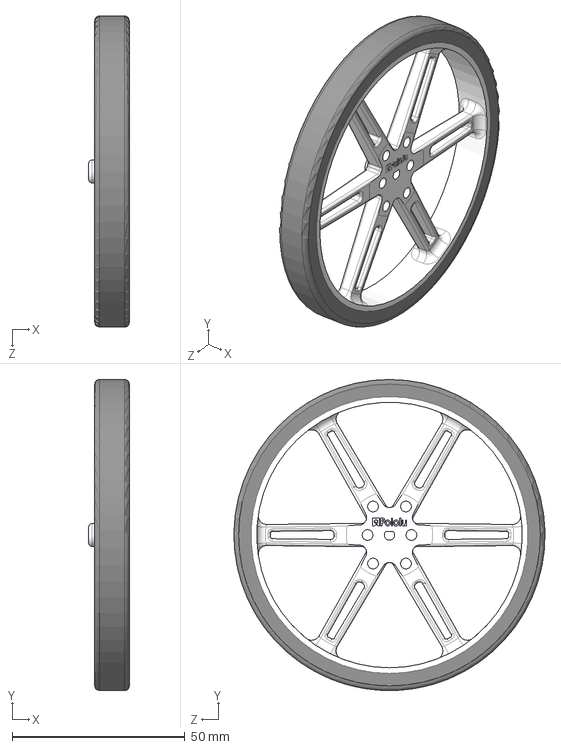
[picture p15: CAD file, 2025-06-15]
Hardware/Mechanical/Solidworks 2024 Part Files/STEP Files/pololu-wheel-90x10mm-white.step
11.8 x 90.0 x 90.0 mm

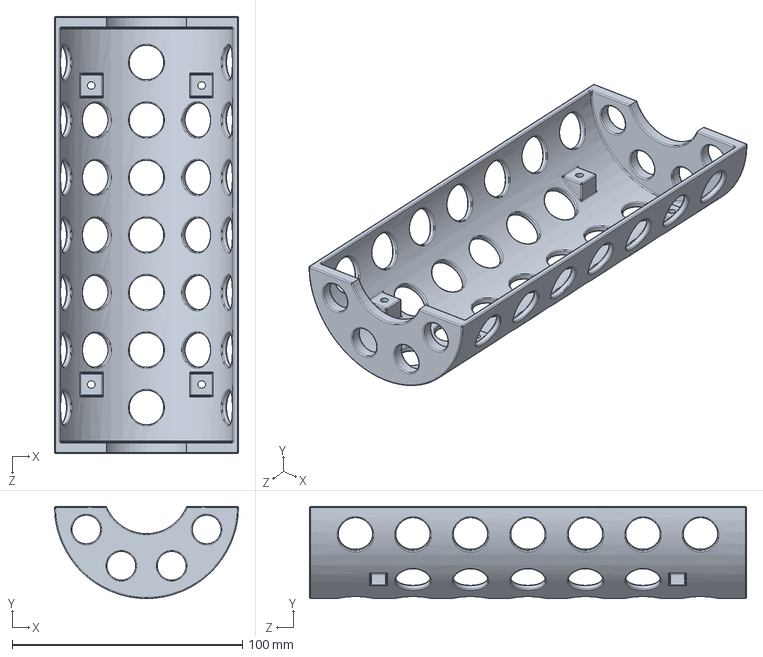
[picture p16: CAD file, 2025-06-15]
Hardware/Mechanical/Solidworks 2024 Part Files/Top Shell.SLDPRT
80.0 x 40.0 x 190.0 mm

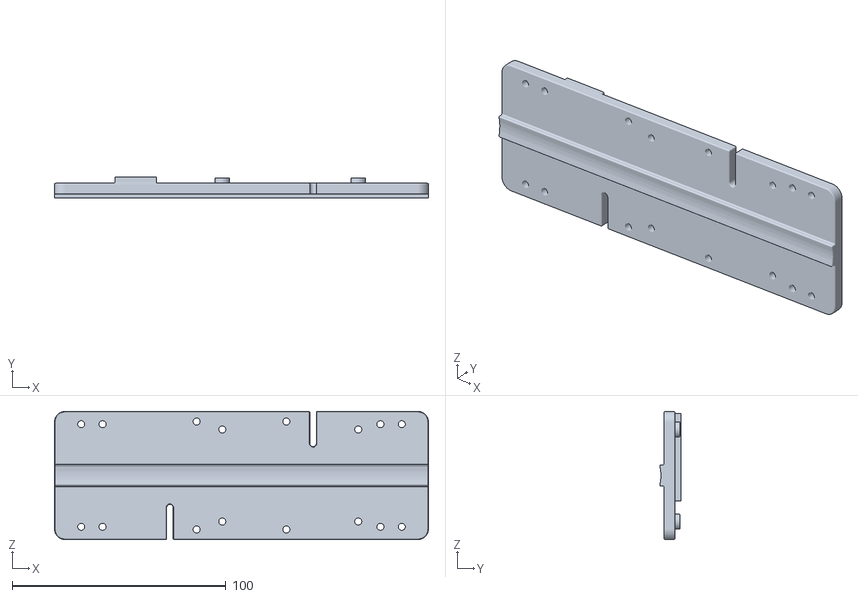
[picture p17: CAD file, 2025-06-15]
Hardware/Mechanical/STL 3-D Print Files/Robot Chassis FIXED.STL
175.0 x 10.0 x 60.0

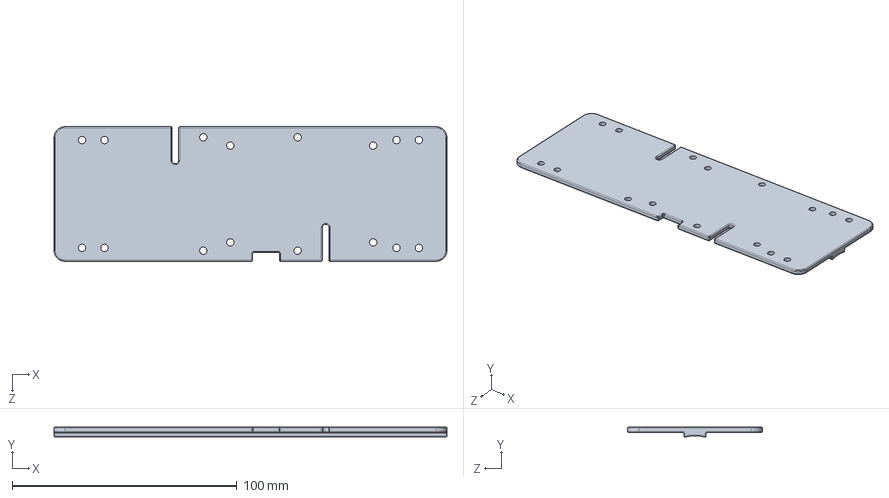
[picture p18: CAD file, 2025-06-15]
Hardware/Mechanical/Solidworks 2024 Part Files/Robot Chassis Bottom Half.SLDPRT
175.0 x 4.52 x 60.0 mm

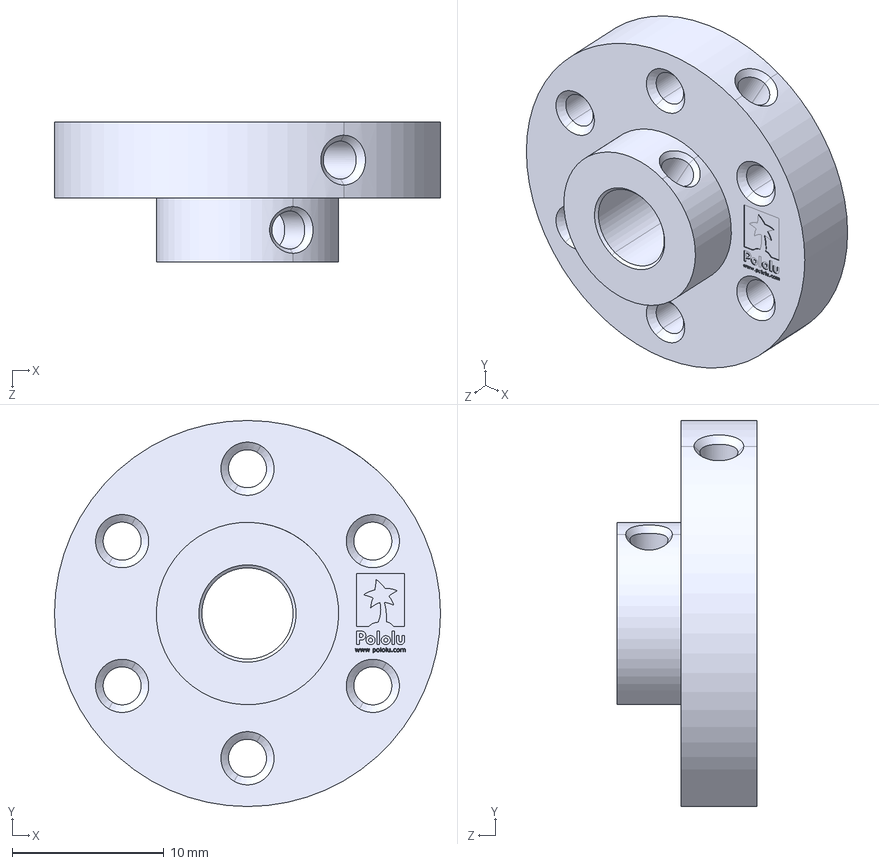
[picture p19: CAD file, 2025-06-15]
Hardware/Mechanical/Solidworks 2024 Part Files/STEP Files/pololu-universal-aluminum-mounting-hub-for-6mm-shaft-m3-holes.step
25.4 x 25.4 x 9.20 mm

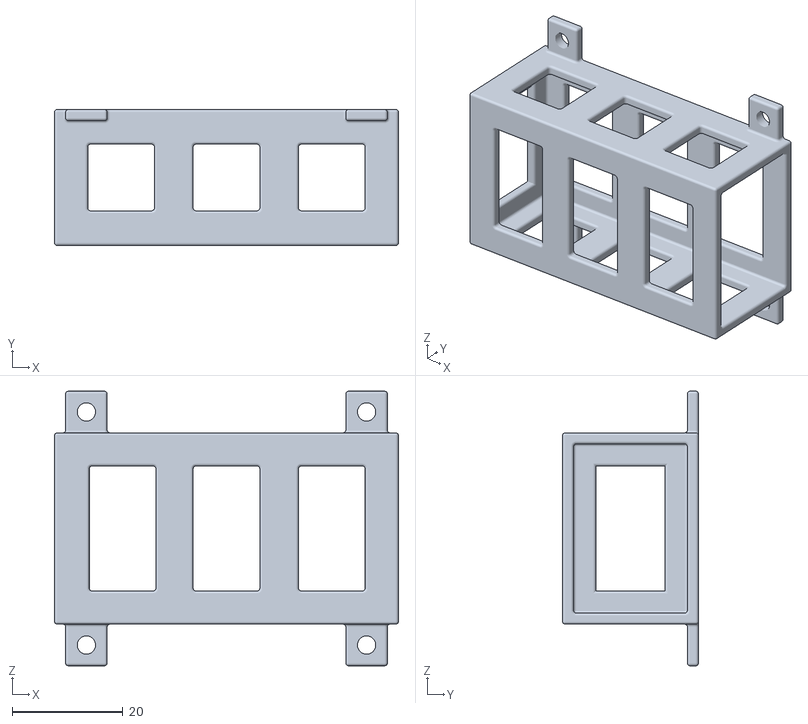
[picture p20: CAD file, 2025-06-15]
Hardware/Mechanical/STL 3-D Print Files/Battery Compartment.STL
62.0 x 24.5 x 49.5

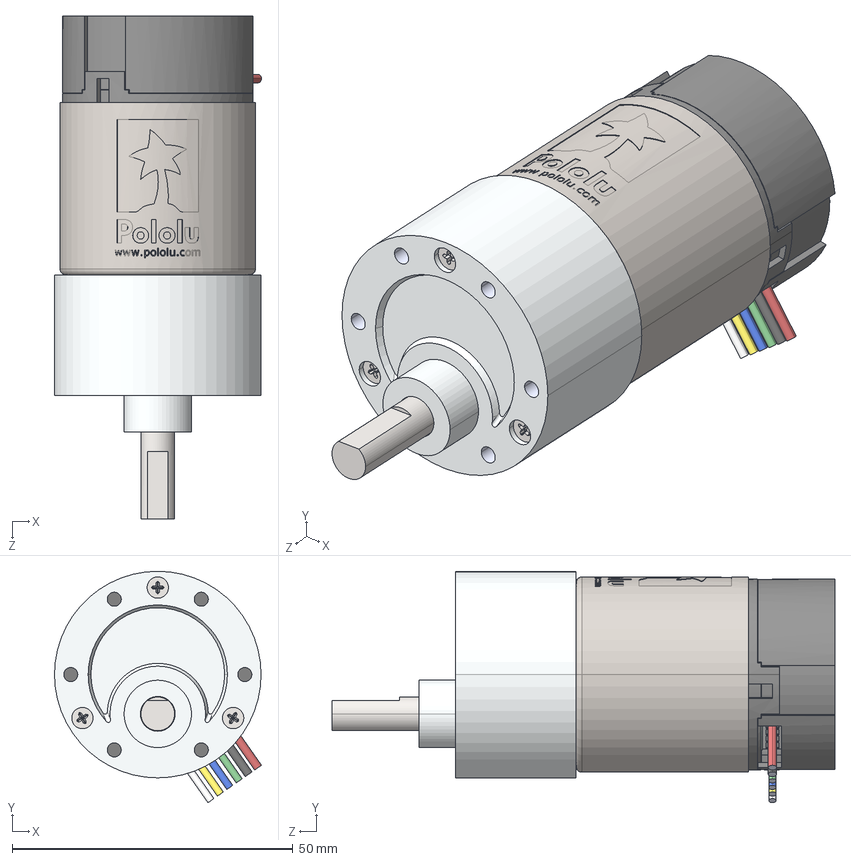
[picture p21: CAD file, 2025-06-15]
Hardware/Mechanical/Solidworks 2024 Part Files/STEP Files/37d-gearmotor-19-30-encoder.step
36.9 x 41.2 x 89.6 mm

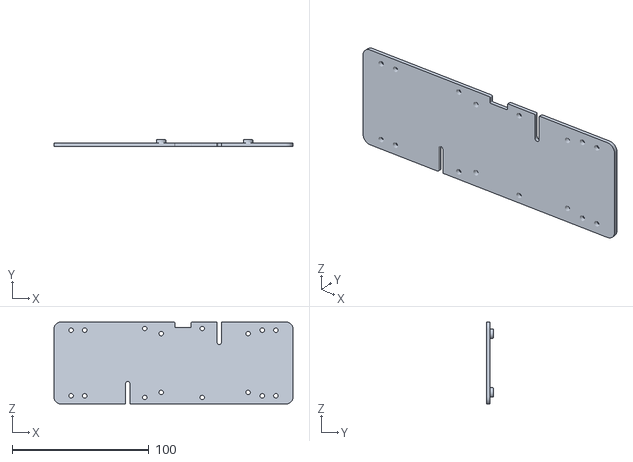
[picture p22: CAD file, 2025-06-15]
Hardware/Mechanical/STL 3-D Print Files/Robot Chassis Top Half No Holder.STL
175.0 x 5.00 x 60.0

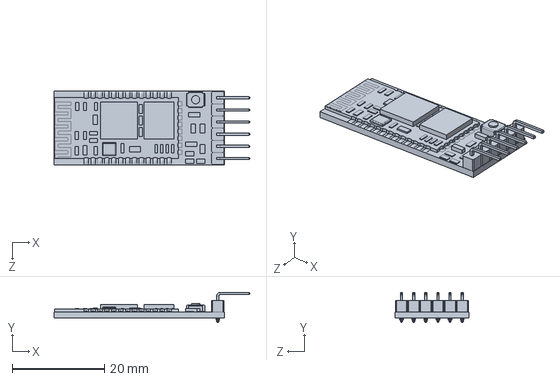
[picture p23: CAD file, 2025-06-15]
Hardware/Mechanical/Solidworks 2024 Part Files/HC-05.SLDPRT
42.6 x 6.55 x 16.0 mm

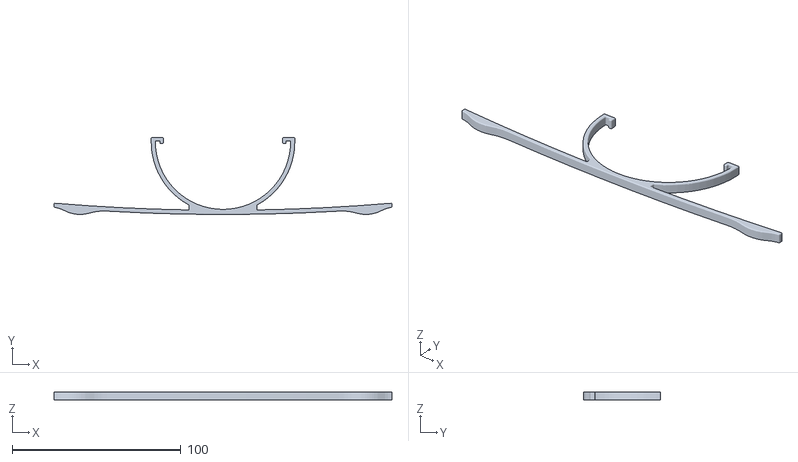
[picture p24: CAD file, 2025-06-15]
Hardware/Mechanical/STL 3-D Print Files/Robot Training Wheels.STL
200.0 x 45.5 x 5.00

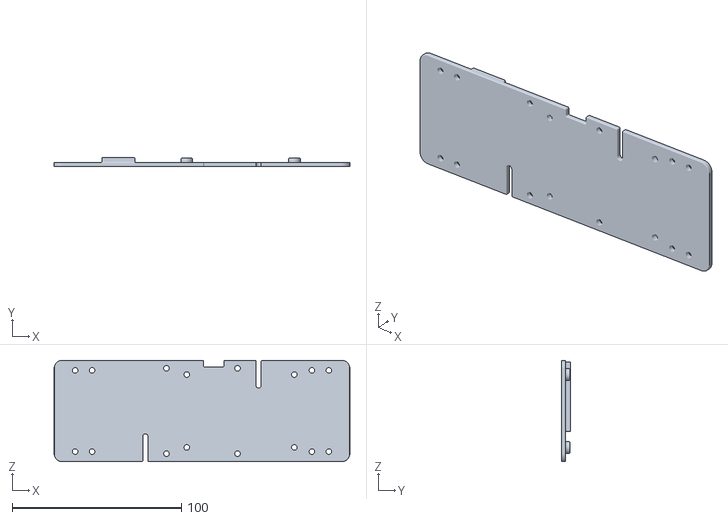
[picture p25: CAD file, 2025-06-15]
Hardware/Mechanical/STL 3-D Print Files/Robot Chassis Top Half.STL
175.0 x 5.50 x 60.0

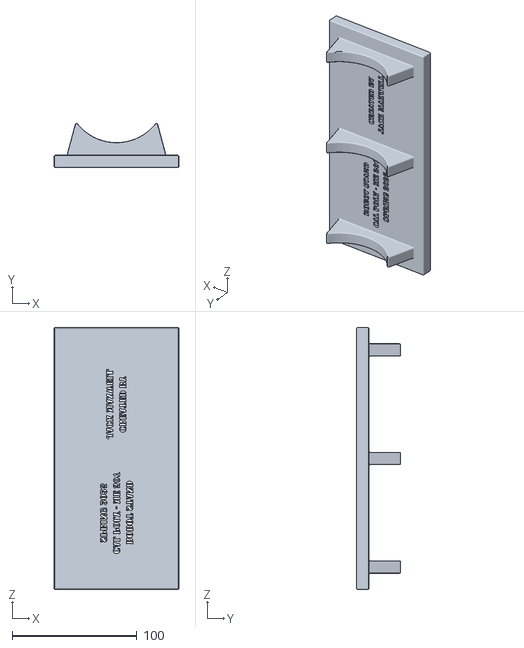
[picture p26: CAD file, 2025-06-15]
Hardware/Mechanical/STL 3-D Print Files/Robot Stand Engraved.STL
100.0 x 35.4 x 210.0

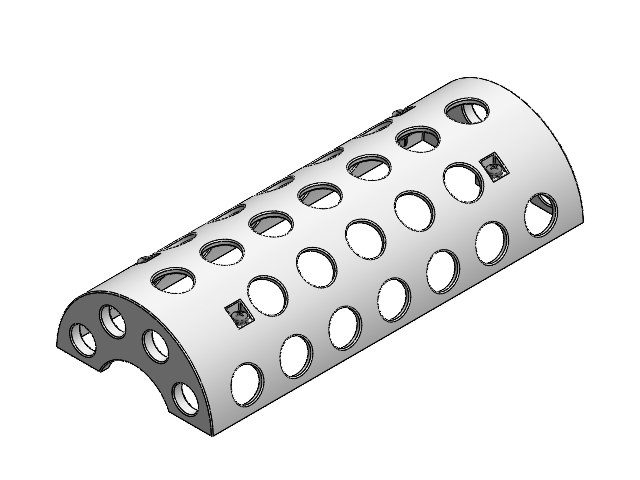
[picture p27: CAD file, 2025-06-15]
Hardware/Mechanical/Solidworks 2024 Part Files/Robot Captain's Quarters.SLDASM
Top Shell
92000A118_Passivated 18-8 Stainless Steel Pan Head Phillips Screws x 4
90940A103_Polycarbonate Plastic Washer x 4
94868A162_Female Threaded Hex Standoff x 4

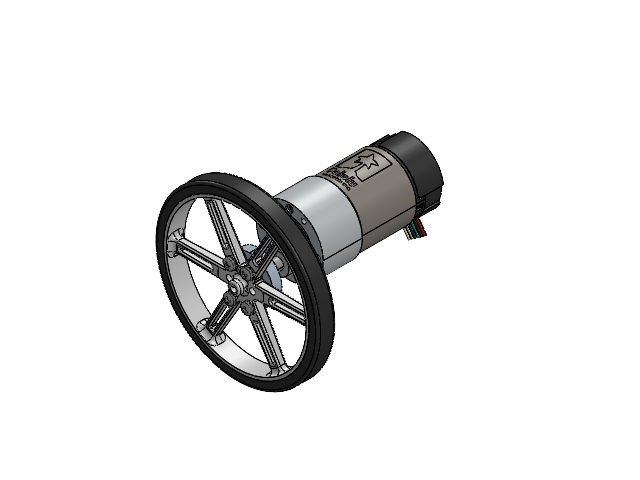
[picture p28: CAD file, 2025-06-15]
Hardware/Mechanical/Solidworks 2024 Part Files/Motor Wheel Assembly.SLDASM
Gear Motor with Encoder
Universal Mounting Hub
Wheel 90mm
90940A103_Polycarbonate Plastic Washer x 4
92000A122_Passivated 18-8 Stainless Steel Pan Head Phillips Screws x 4

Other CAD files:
Hardware/Mechanical/Solidworks 2024 Part Files/Battery Assembly.SLDASM
Hardware/Mechanical/Solidworks 2024 Part Files/Robot Chassis.SLDPRT
Hardware/Mechanical/STL 3-D Print Files/Robot Chassis Bottom Half.STL
Hardware/Mechanical/Solidworks 2024 Part Files/Universal Mounting Hub.SLDPRT
Hardware/Mechanical/STL 3-D Print Files/HC-05 Holder.STL
Hardware/Mechanical/STL 3-D Print Files/Robot Chassis FIXED AGAIN.STL
Hardware/Mechanical/STL 3-D Print Files/Robot Chassis.STL
Hardware/Mechanical/STL 3-D Print Files/Robot Stand.STL
Hardware/Mechanical/Solidworks 2024 Part Files/Battery Compartment.SLDPRT
Hardware/Mechanical/Solidworks 2024 Part Files/Bottom Shell.SLDPRT
Hardware/Mechanical/Solidworks 2024 Part Files/Gear Motor with Encoder.SLDPRT
Hardware/Mechanical/Solidworks 2024 Part Files/Gens Ace Lipo Battery Pack.SLDPRT
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

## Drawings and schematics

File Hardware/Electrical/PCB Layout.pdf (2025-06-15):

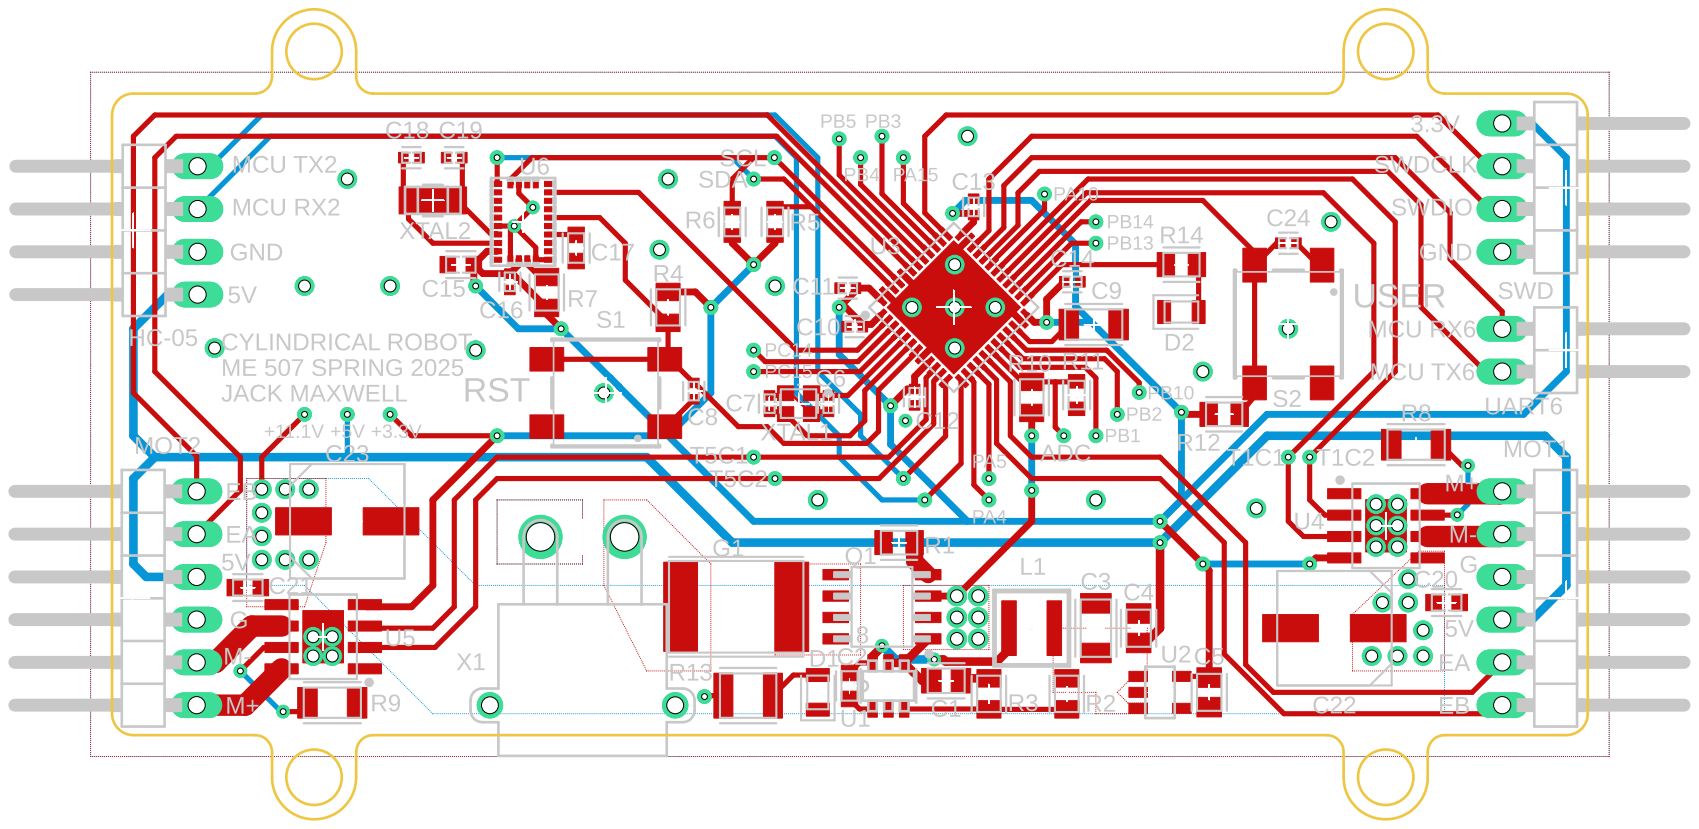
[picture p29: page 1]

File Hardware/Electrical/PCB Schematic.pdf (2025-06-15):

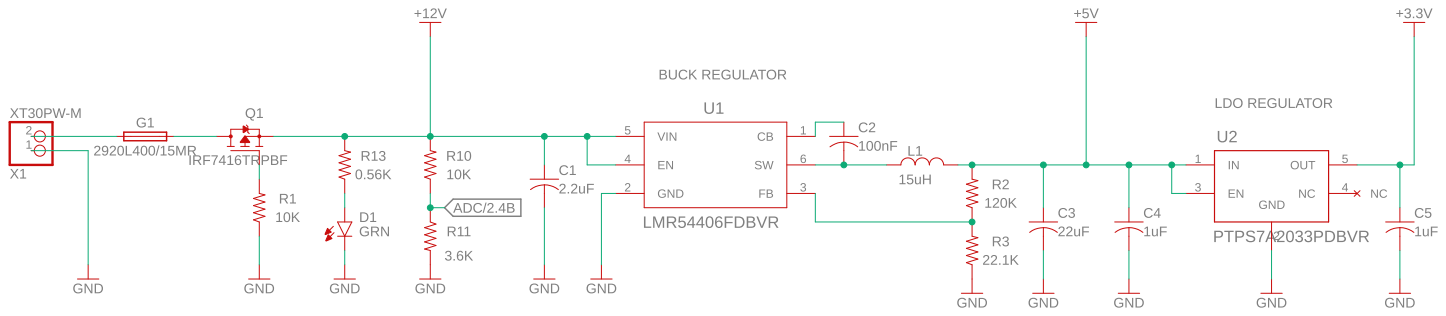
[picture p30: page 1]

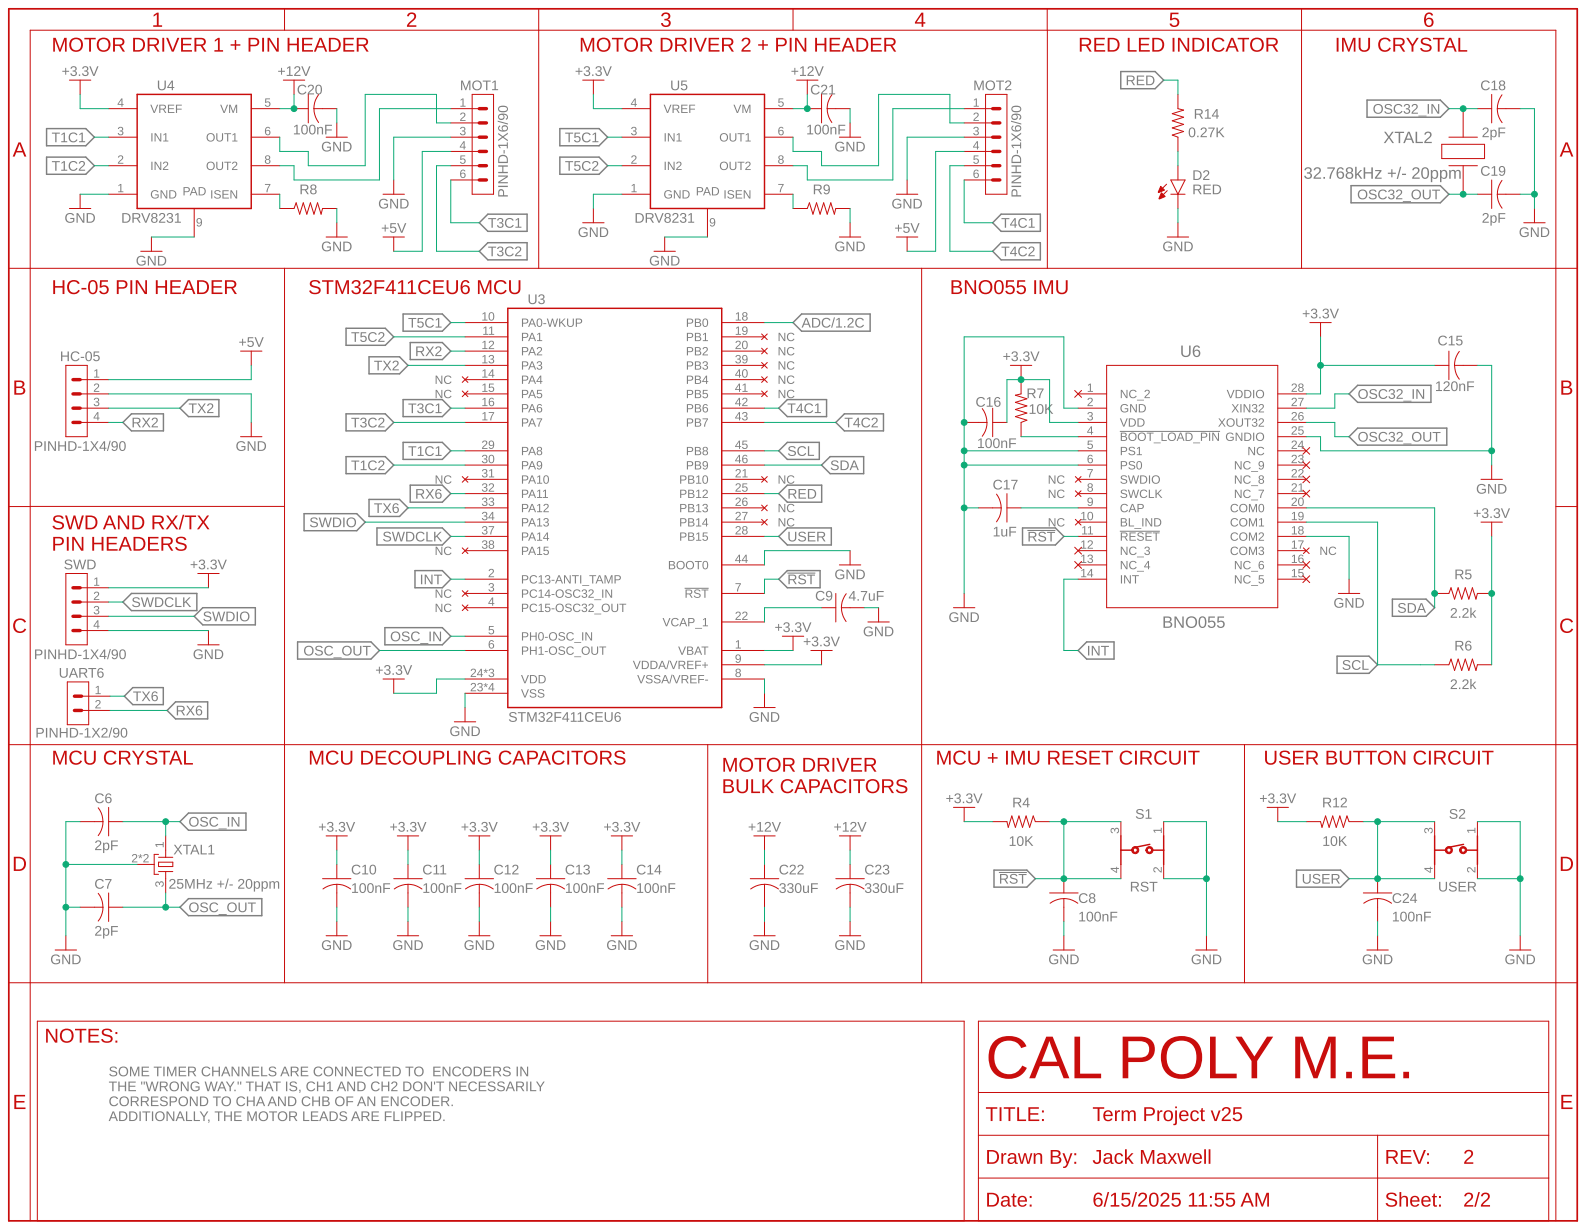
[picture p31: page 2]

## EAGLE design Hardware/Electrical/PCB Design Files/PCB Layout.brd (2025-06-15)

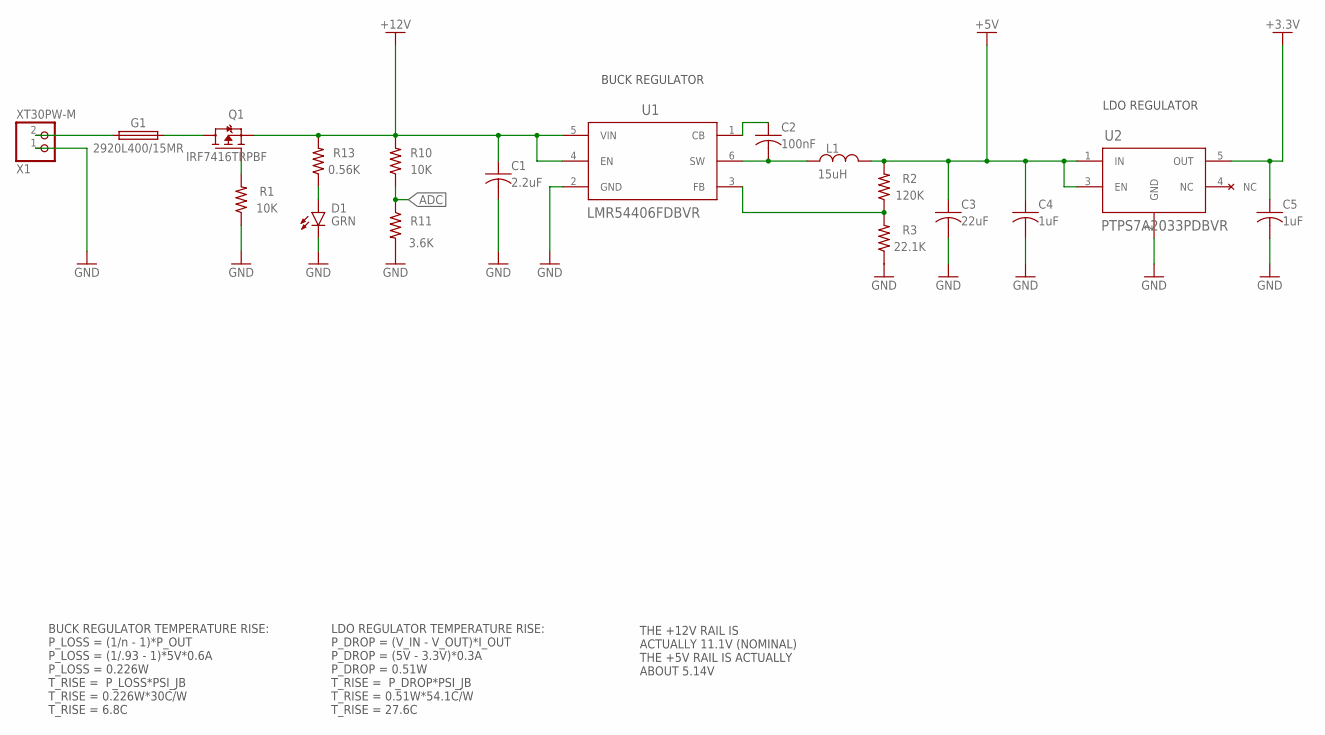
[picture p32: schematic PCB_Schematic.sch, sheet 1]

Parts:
C1: 2.2uF; CAPC2012X110
C2: 100nF; CAPC1608X85
C3: 22uF; CAPC3216X135
C4, C5: 1uF; CAPC2012X110
D1: GRN; LEDC2012X110N_FLAT-G
G1: 2920L400/15MR; FUSC7351X160
L1: 15uH; IND_XGL4040_COC
Q1: IRF7416TRPBF; SO-8
R1, R10: 10K; RESC2012X65
R2: 120K; RESC2012X65
R3: 22.1K; RESC2012X65
R11: 3.6K; RESC1608X60
R13: 0.56K; RESC3224X71
U1: LMR54406FDBVR; LMR54406DBVR_TEX
U2: PTPS7A2033PDBVR; DBV0005A-MFG
X1: XT30PW-M

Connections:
+3.3V: C5.1, U2.5 (OUT); also elsewhere on the board
+5V: C3.1, C4.1, L1.2, R2.2, U2.1 (IN), U2.3 (EN); also elsewhere on the board
+12V: C1.1, Q1.1 (S), Q1.2 (S), Q1.3 (S), R10.2, R13.2, U1.4 (EN), U1.5 (VIN); also elsewhere on the board
ADC: R10.1, R11.1; also elsewhere on the board
GND: C1.2, C3.2, C4.2, C5.2, D1.C, R1.1, R3.1, R11.2, U1.2 (GND), U2.2 (GND), X1.1; also elsewhere on the board
unnamed: C2.1, U1.1 (CB)
unnamed: C2.2, L1.1, U1.6 (SW)
unnamed: Q1.4 (G), R1.2
unnamed: R2.1, R3.2, U1.3 (FB)
unnamed: G1.1, X1.2
unnamed: G1.2, Q1.5 (D), Q1.6 (D), Q1.7 (D), Q1.8 (D)
unnamed: D1.A, R13.1

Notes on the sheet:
BUCK REGULATOR
LDO REGULATOR
BUCK REGULATOR TEMPERATURE RISE: P_LOSS = (1/n - 1)*P_OUT P_LOSS = (1/.93 - 1)*5V*0.6A P_LOSS = 0.226W T_RISE = P_LOSS*PSI_JB T_RISE = 0.226W*30C/W T_RISE = 6.8C
LDO REGULATOR TEMPERATURE RISE: P_DROP = (V_IN - V_OUT)*I_OUT P_DROP = (5V - 3.3V)*0.3A P_DROP = 0.51W T_RISE = P_DROP*PSI_JB T_RISE = 0.51W*54.1C/W T_RISE = 27.6C
THE +12V RAIL IS ACTUALLY 11.1V (NOMINAL) THE +5V RAIL IS ACTUALLY ABOUT 5.14V

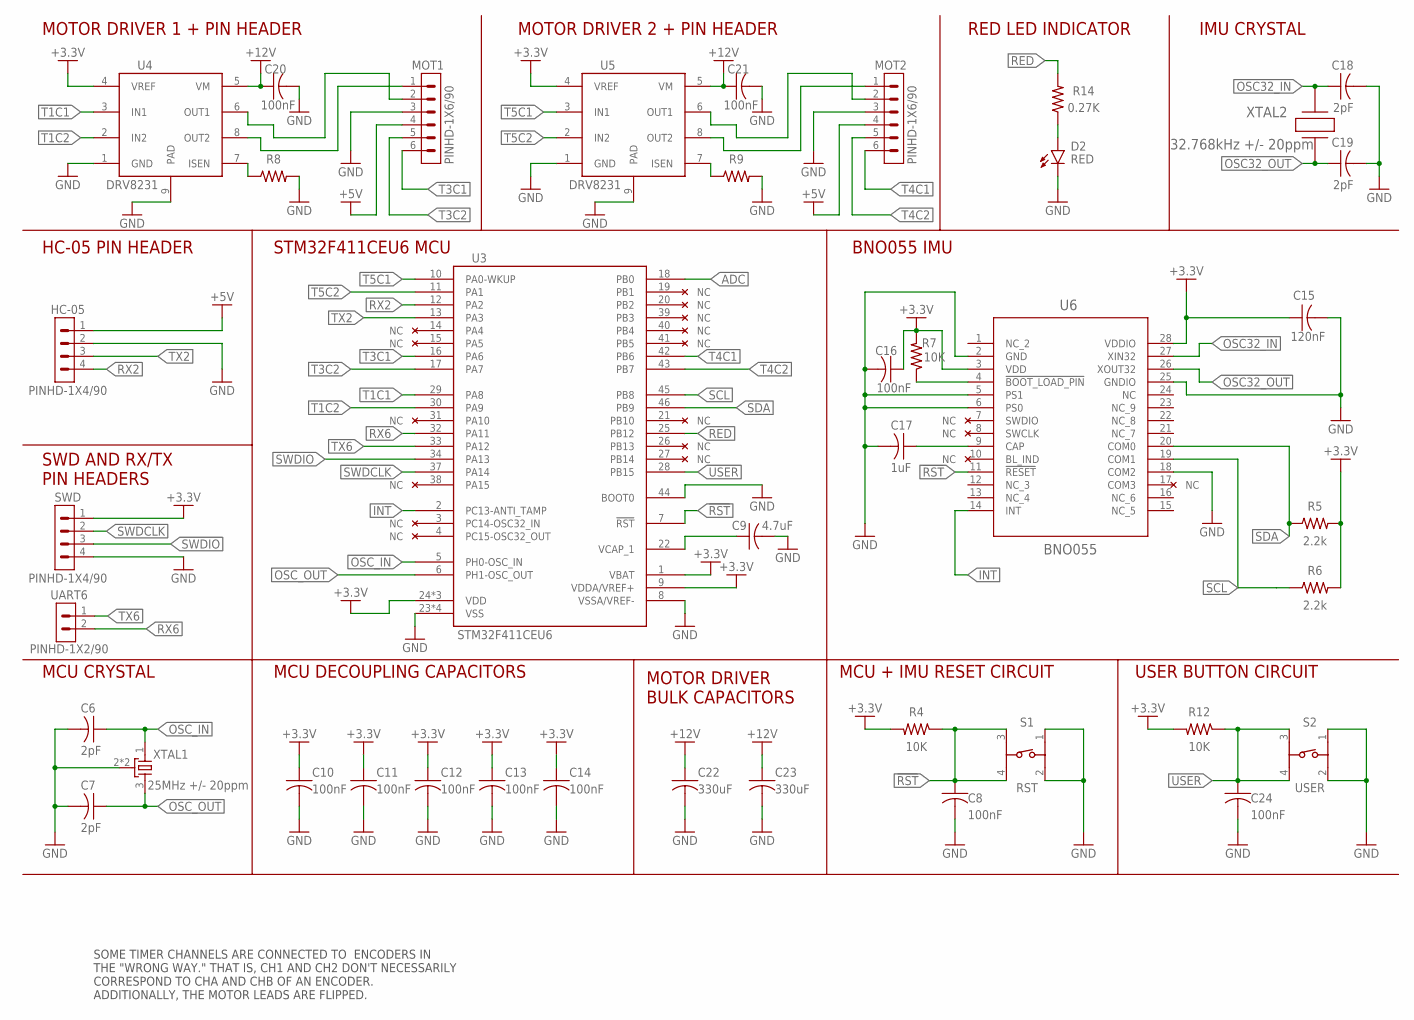
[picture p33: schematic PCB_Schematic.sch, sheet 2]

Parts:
C6, C7, C18, C19: 2pF; CAPC1005X60
C8, C10, C11, C12, C13, C14, C16, C24: 100nF; CAPC1005X60
C9: 4.7uF; CAPC3216X135
C15: 120nF; CAPC1608X85
C17: 1uF; CAPC1608X85
C20, C21: 100nF; CAPC1608X85
C22, C23: 330uF; CAPAE660X800N
D2: RED; LEDC2012X110N_FLAT-R
HC-05: PINHD-1X4/90; 1X04/90
MOT1, MOT2: PINHD-1X6/90; 1X06/90
R4, R7, R12: 10K; RESC2012X65
R5, R6: 2.2k; RESC1608X60
R8, R9: R-US_CHIP-1206(3216-METRIC); RESC3216X70
R14: 0.27K; RESC2012X65
S1: RST; 430481035816
S2: USER; 430481035816
SWD: PINHD-1X4/90; 1X04/90
U3: STM32F411CEU6; QFN50P700X700X100-48N
U4, U5: DRV8231; DRV8231DDAR
U6: BNO055; QFN_BNO055_BOS
UART6: PINHD-1X2/90; 1X02/90
XTAL1: 25MHz +/- 20ppm; OSCCC200X160X50N
XTAL2: 32.768kHz +/- 20ppm; CHIP_NX3215S_NDK

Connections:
!RST!: C8.1, R4.1, S1.3, S1.4, U3.7 (!RST), U6.11 (!RESET)
+3.3V: C10.1, C11.1, C12.1, C13.1, C14.1, C15.1, C16.1, R4.2, R5.2, R6.2, R7.2, R12.2, SWD.1, U3.1 (VBAT), U3.9 (VDDA/VREF+), U3.24 (VDD), U3.36 (VDD), U3.48 (VDD), U4.4 (VREF), U5.4 (VREF), U6.3 (VDD), U6.28 (VDDIO); also elsewhere on the board
+5V: HC-05.1, MOT1.4, MOT2.4; also elsewhere on the board
+12V: C20.1, C21.1, C22.1, C23.1, U4.5 (VM), U5.5 (VM); also elsewhere on the board
ADC: U3.18 (PB0); also elsewhere on the board
GND: C6.2, C7.2, C8.2, C9.2, C10.2, C11.2, C12.2, C13.2, C14.2, C15.2, C16.2, C17.2, C18.2, C19.2, C20.2, C21.2, C22.2, C23.2, C24.2, D2.C, HC-05.2, MOT1.3, MOT2.3, R8.2, R9.2, S1.1, S1.2, S2.1, S2.2, SWD.4, U3.8 (VSSA/VREF-), U3.23 (VSS), U3.35 (VSS), U3.44 (BOOT0), U3.47 (VSS), U3.49 (VSS), U4.1 (GND), U4.9 (PAD), U5.1 (GND), U5.9 (PAD), U6.2 (GND), U6.5 (PS1), U6.6 (PS0), U6.18 (COM2), U6.25 (GNDIO), XTAL1.2 (GND), XTAL1.4 (GND); also elsewhere on the board
INT: U3.2 (PC13-ANTI_TAMP), U6.14 (INT)
unnamed: MOT1.2, U4.6 (OUT1)
unnamed: MOT1.1, U4.8 (OUT2)
unnamed: C17.1, U6.9 (CAP)
unnamed: R7.1, U6.4 (!BOOT_LOAD_PIN)
unnamed: R8.1, U4.7 (ISEN)
unnamed: MOT2.2, U5.6 (OUT1)
unnamed: MOT2.1, U5.8 (OUT2)
unnamed: D2.A, R14.1
unnamed: R9.1, U5.7 (ISEN)
OSC32_IN: C18.1, U6.27 (XIN32), XTAL2.2
OSC32_OUT: C19.1, U6.26 (XOUT32), XTAL2.1
OSC_IN: C6.1, U3.5 (PH0-OSC_IN), XTAL1.1
OSC_OUT: C7.1, U3.6 (PH1-OSC_OUT), XTAL1.3 (2)
RED: R14.2, U3.25 (PB12)
RX2: HC-05.4, U3.12 (PA2)
RX6: U3.32 (PA11), UART6.2
SCL: R6.1, U3.45 (PB8), U6.19 (COM1)
SDA: R5.1, U3.46 (PB9), U6.20 (COM0)
SWDCLK: SWD.2, U3.37 (PA14)
SWDIO: SWD.3, U3.34 (PA13)
T1C1: U3.29 (PA8), U4.3 (IN1)
T1C2: U3.30 (PA9), U4.2 (IN2)
T3C1: MOT1.6, U3.16 (PA6)
T3C2: MOT1.5, U3.17 (PA7)
T4C1: MOT2.6, U3.42 (PB6)
T4C2: MOT2.5, U3.43 (PB7)
T5C1: U3.10 (PA0-WKUP), U5.3 (IN1)
T5C2: U3.11 (PA1), U5.2 (IN2)
TX2: HC-05.3, U3.13 (PA3)
TX6: U3.33 (PA12), UART6.1
USER: C24.1, R12.1, S2.3, S2.4, U3.28 (PB15)
VCAP_1: C9.1, U3.22 (VCAP_1)

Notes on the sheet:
MOTOR DRIVER 1 + PIN HEADER
MOTOR DRIVER 2 + PIN HEADER
IMU CRYSTAL
BNO055 IMU
MCU + IMU RESET CIRCUIT
MCU DECOUPLING CAPACITORS
STM32F411CEU6 MCU
HC-05 PIN HEADER
SWD AND RX/TX PIN HEADERS
MCU CRYSTAL
MOTOR DRIVER BULK CAPACITORS
USER BUTTON CIRCUIT
RED LED INDICATOR
SOME TIMER CHANNELS ARE CONNECTED TO ENCODERS IN THE "WRONG WAY." THAT IS, CH1 AND CH2 DON'T NECESSARILY CORRESPOND TO CHA AND CHB OF AN ENCODER. ADDITIONALLY, THE MOTOR LEADS ARE FLIPPED.

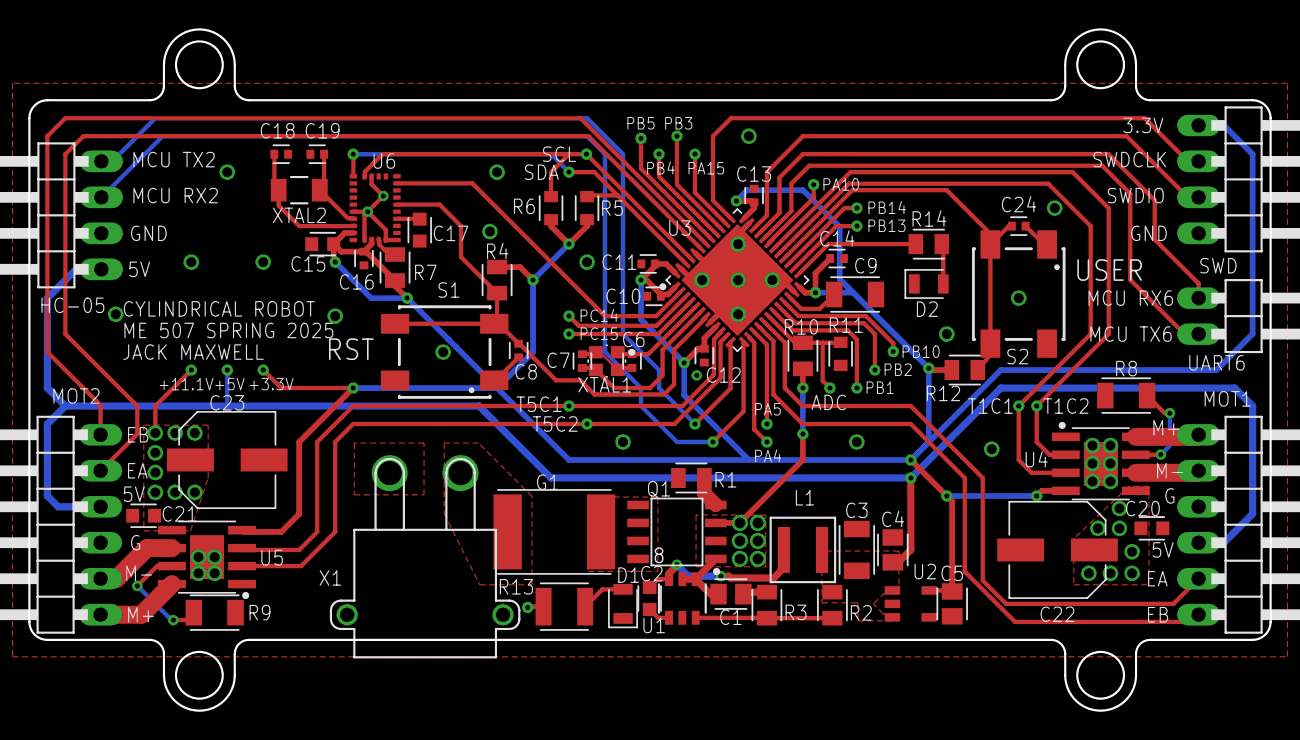
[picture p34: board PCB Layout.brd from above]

Board: 2 copper layers, 87.6 x 48.1 mm, 59 parts (0 on the bottom side), 46 nets.

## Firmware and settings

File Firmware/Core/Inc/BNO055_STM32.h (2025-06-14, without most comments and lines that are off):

#ifdef __cplusplus
extern "C" {
#endif
#define INC_BNO055_STM32_H_
#include <stdint.h>
#include <stdio.h>
#include "stm32f4xx_hal.h"
#include <stdbool.h>
extern I2C_HandleTypeDef hi2c1;
#define bno_i2c (hi2c1)
#define P_BNO055 				    (0x29<<1)
#define BNO055_ID 					0xA0
#define MAG_RADIUS_MSB_ADDR 		0x6A
#define MAG_RADIUS_LSB_ADDR 		0x69
#define ACC_RADIUS_MSB_ADDR 		0x68
#define ACC_RADIUS_LSB_ADDR 		0x67
#define GYRO_OFFSET_Z_MSB_ADDR 		0x66
#define GYRO_OFFSET_Z_LSB_ADDR 		0x65
#define GYRO_OFFSET_Y_MSB_ADDR 		0x64
#define GYRO_OFFSET_Y_LSB_ADDR 		0x63
#define GYRO_OFFSET_X_MSB_ADDR 		0x62
#define GYRO_OFFSET_X_LSB_ADDR 		0x61
#define MAG_OFFSET_Z_MSB_ADDR 		0x60
#define MAG_OFFSET_Z_LSB_ADDR 		0x5F
#define MAG_OFFSET_Y_MSB_ADDR 		0x5E
#define MAG_OFFSET_Y_LSB_ADDR 		0x5D
#define MAG_OFFSET_X_MSB_ADDR 		0x5C
#define MAG_OFFSET_X_LSB_ADDR 		0x5B
#define ACC_OFFSET_Z_MSB_ADDR 		0x5A
#define ACC_OFFSET_Z_LSB_ADDR 		0x59
#define ACC_OFFSET_Y_MSB_ADDR 		0x58
#define ACC_OFFSET_Y_LSB_ADDR 		0x57
#define ACC_OFFSET_X_MSB_ADDR 		0x56
#define ACC_OFFSET_X_LSB_ADDR 		0x55
#define AXIS_MAP_SIGN_ADDR 			0x42
#define AXIS_MAP_CONFIG_ADDR 		0x41
#define TEMP_SOURCE_ADDR			0x40
#define SYS_TRIGGER_ADDR 			0x3F
#define PWR_MODE_ADDR 				0x3E
#define OPR_MODE_ADDR 				0x3D
#define UNIT_SEL_ADDR 				0x3B
#define SYS_ERR_ADDR				0x3A
#define SYS_STATUS_ADDR				0x39
#define SYS_CLK_STATUS_ADDR			0x38
#define INT_STA_ADDR				0x37
#define ST_RESULT_ADDR				0x36
#define CALIB_STAT_ADDR 			0x35
#define TEMP_ADDR					0x34
#define GRV_DATA_Z_MSB_ADDR 		0x33
#define GRV_DATA_Z_LSB_ADDR 		0x32
#define GRV_DATA_Y_MSB_ADDR 		0x31
#define GRV_DATA_Y_LSB_ADDR 		0x30
#define GRV_DATA_X_MSB_ADDR 		0x2F
#define GRV_DATA_X_LSB_ADDR 		0x2E
#define GRV_DATA_BASEADDR			GRV_DATA_X_LSB_ADDR
#define LIA_DATA_Z_MSB_ADDR 		0x2D
#define LIA_DATA_Z_LSB_ADDR 		0x2C
#define LIA_DATA_Y_MSB_ADDR 		0x2B
#define LIA_DATA_Y_LSB_ADDR 		0x2A
#define LIA_DATA_X_MSB_ADDR 		0x29
#define LIA_DATA_X_LSB_ADDR 		0x28
#define LIA_DATA_BASEADDR			LIA_DATA_X_LSB_ADDR
#define QUA_DATA_Z_MSB_ADDR 		0x27
#define QUA_DATA_Z_LSB_ADDR 		0x26
#define QUA_DATA_Y_MSB_ADDR 		0x25
#define QUA_DATA_Y_LSB_ADDR 		0x24
#define QUA_DATA_X_MSB_ADDR 		0x23
#define QUA_DATA_X_LSB_ADDR 		0x22
#define QUA_DATA_W_MSB_ADDR 		0x21
#define QUA_DATA_W_LSB_ADDR 		0x20
#define QUA_DATA_BASEADDR			QUA_DATA_W_LSB_ADDR
#define EUL_PITCH_MSB_ADDR 			0x1F
#define EUL_PITCH_LSB_ADDR 			0x1E
#define EUL_ROLL_MSB_ADDR 			0x1D
#define EUL_ROLL_LSB_ADDR 			0x1C
#define EUL_HEADING_MSB_ADDR 		0x1B
#define EUL_HEADING_LSB_ADDR 		0x1A
#define EUL_DATA_BASEADDR			EUL_HEADING_LSB_ADDR
#define GYRO_DATA_Z_MSB_ADDR 		0x19
#define GYRO_DATA_Z_LSB_ADDR 		0x18
#define GYRO_DATA_Y_MSB_ADDR 		0x17
#define GYRO_DATA_Y_LSB_ADDR 		0x16
#define GYRO_DATA_X_MSB_ADDR 		0x15
#define GYRO_DATA_X_LSB_ADDR 		0x14
#define GYRO_DATA_BASEADDR			GYRO_DATA_X_LSB_ADDR
#define MAG_DATA_Z_MSB_ADDR 		0x13
#define MAG_DATA_Z_LSB_ADDR 		0x12
#define MAG_DATA_Y_MSB_ADDR 		0x11
#define MAG_DATA_Y_LSB_ADDR 		0x10
#define MAG_DATA_X_MSB_ADDR 		0x0F
#define MAG_DATA_X_LSB_ADDR 		0x0E
#define MAG_DATA_BASEADDR			MAG_DATA_X_LSB_ADDR
#define ACCEL_DATA_Z_MSB_ADDR 		0x0D
#define ACCEL_DATA_Z_LSB_ADDR 		0x0C
#define ACCEL_DATA_Y_MSB_ADDR 		0x0B
#define ACCEL_DATA_Y_LSB_ADDR 		0x0A
#define ACCEL_DATA_X_MSB_ADDR 		0x09
#define ACCEL_DATA_X_LSB_ADDR 		0x08
#define ACCEL_DATA_BASEADDR		ACCEL_DATA_X_LSB_ADDR
#define PAGE_ID_ADDR 				0x07
#define BL_REV_ID_ADDR				0x06
#define SW_REV_ID_MSB_ADDR			0x05
#define SW_REV_ID_LSB_ADDR			0x04
#define GYR_ID_ADDR					0x03
#define MAG_ID_ADDR					0x02
#define ACC_ID_ADDR					0x01
#define CHIP_ID_ADDR 				0x00
#define UNIQUE_ID_BASEADDR			0x50
#define GYR_AM_SET_ADDR 			0x1F
#define GYR_AM_THRES_ADDR 			0x1E
#define GYR_DUR_Z_ADDR 				0x1D
#define GYR_HR_Z_SET_ADDR 			0x1C
#define GYR_DUR_Y_ADDR 				0x1B
#define GYR_HR_Y_SET_ADDR 			0x1A
#define GYR_DUR_X_ADDR 				0x19
#define GYR_HR_X_SET_ADDR 			0x18
#define GYR_INT_SETING_ADDR 		0x17
#define ACC_NM_SET_ADDR 			0x16
#define ACC_NM_THRES_ADDR 			0x15
#define ACC_HG_THRES_ADDR 			0x14
#define ACC_HG_DURATION_ADDR 		0x13
#define ACC_INT_Setting_ADDR 		0x12
#define ACC_AM_THRES_ADDR 			0x11
#define INT_EN_ADDR 				0x10
#define INT_MSK_ADDR 				0x0F
#define GYR_Sleep_Config_ADDR 		0x0D
#define ACC_Sleep_Config_ADDR 		0x0C
#define GYRO_CONFIG_1_ADDR 			0x0B
#define GYRO_CONFIG_0_ADDR 			0x0A
#define MAG_CONFIG_ADDR 			0x09
#define ACC_CONFIG_ADDR 			0x08
#define PAGE_0 						0x00
#define PAGE_1 						0x01
typedef struct{
	uint8_t STresult;	//First 4 bit[0:3] indicates self test resulst 3:ST_MCU, 2:ST_GYRO, 1:ST_MAG, 0:ST_ACCEL
	uint8_t SYSError;	//Contains system error type If SYSStatus is System_Error(0x01)
	uint8_t SYSStatus;
}BNO_Status_t;
typedef struct{
	uint8_t System;
	uint8_t Gyro;
	uint8_t Acc;
	uint8_t MAG;
}Calib_status_t;
typedef struct{ //SENSOR DATA AXIS X, Y and Z
	float X;
	float Y;
	float Z;
}BNO055_Data_XYZ_t;
typedef struct{ //SENSOR DATA AXIS W, X, Y and Z (Only for quaternion data)
	float W;
	float X;
	float Y;
	float Z;
}BNO055_QuaData_WXYZ_t;
typedef struct{ //SENSOR DATAS
	BNO055_Data_XYZ_t Accel;
	BNO055_Data_XYZ_t Gyro;
	BNO055_Data_XYZ_t Magneto;
	BNO055_Data_XYZ_t Euler;
	BNO055_Data_XYZ_t LineerAcc;
	BNO055_Data_XYZ_t Gravity;
	BNO055_QuaData_WXYZ_t Quaternion;
}BNO055_Sensors_t;
typedef enum {
    SENSOR_GRAVITY     = 0x01,
    SENSOR_QUATERNION  = 0x02,
    SENSOR_LINACC      = 0x04,
    SENSOR_GYRO        = 0x08,
    SENSOR_ACCEL       = 0x10,
    SENSOR_MAG         = 0x20,
    SENSOR_EULER       = 0x40,
} BNO055_Sensor_Type;
#define BNO_ACCEL 					ACCEL_DATA_BASEADDR
#define BNO_GYRO 					GYRO_DATA_BASEADDR
#define BNO_MAG 					MAG_DATA_BASEADDR
#define BNO_EULER 					EUL_DATA_BASEADDR
#define BNO_LINACC 					LIA_DATA_BASEADDR
#define BNO_GRAVITY					GRV_DATA_BASEADDR
#define BNO_QUATERNION				QUA_DATA_BASEADDR
typedef struct
{
	uint8_t Unit_Sel;
	uint8_t Axis;
	uint8_t Axis_sign;
	uint8_t Mode;
	uint8_t OP_Modes;
	uint8_t Clock_Source;
	uint8_t ACC_Range;
}BNO055_Init_t;
typedef enum{// OPERATION MODES
	CONFIG_MODE =0x00,		//This is the only mode in which all the writable register map entries can be changed (Except INT , INT_MASK, OPR_MODE)
	ACC_ONLY =0x01,
	MAG_ONLY =0x02,
	GYRO_ONLY =0x03,
	ACC_MAG =0x04,
	ACC_GYRO =0x05,
	MAG_GYRO =0x06,
	AMG= 0x07,
	IMU= 0x08,
	COMPASS =0x09,
	M4G= 0x0A,
	NDOF_FMC_OFF =0x0B,
	NDOF= 0x0C
}Op_Modes_t;
#define BNO055_NORMAL_MODE			0
#define BNO055_LOWPOWER_MODE		1
#define BNO055_SUSPEND_MODE			2
#define DEFAULT_AXIS_REMAP			0x24
#define DEFAULT_AXIS_SIGN			0x00
#define CLOCK_EXTERNAL				(1 << 7)
#define CLOCK_INTERNAL				(0 << 7)
#define UNIT_ORI_ANDROID 			(1 << 7)
#define UNIT_ORI_WINDOWS 			(0 << 7)
#define UNIT_TEMP_CELCIUS 			(0 << 4)
#define UNIT_TEMP_FAHRENHEIT 		(1 << 4)
#define UNIT_EUL_DEG 				(0 << 2)
#define UNIT_EUL_RAD 				(1 << 2)
#define UNIT_GYRO_DPS 				(0 << 1)
#define UNIT_GYRO_RPS 				(1 << 1)
#define UNIT_ACC_MS2				(0 << 0)
#define UNIT_ACC_MG 				(1 << 0)
#define Range_2G 					0x00
#define Range_4G 					0x01
#define Range_8G 					0x02
#define Range_16G 					0x03
void getCalibration(Calib_status_t *calib);
Op_Modes_t getCurrentMode(void);
bool isFullyCalibrated(void);
void setSensorOffsets(const uint8_t *calibData) ;
void getSensorOffsets(uint8_t *calibData);
bool Calibrate_BNO055(void);
void Set_Operation_Mode(Op_Modes_t Mode);
void Clock_Source(uint8_t source);
void SetPowerMODE(uint8_t BNO055_);
void BNO055_Axis(uint8_t remap, uint8_t sign);
void SelectPage(uint8_t page);
void SET_Accel_Range(uint8_t range);
void BNO055_Init(BNO055_Init_t Init);
void ReadData(BNO055_Sensors_t *sensorData,BNO055_Sensor_Type sensors);
void Check_Status(BNO_Status_t *result);
void ResetBNO055(void);
#ifdef __cplusplus
}
#endif

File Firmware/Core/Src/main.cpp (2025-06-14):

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
/* Includes ------------------------------------------------------------------*/
#include "main.h"

/* USER CODE BEGIN Includes */
#include "motor_driver.h"
#include "encoder.h"
#include "time_utils.h"
#include "BNO055_STM32.h"
#include "bno055_init.h"

#include "uart_dma_idle.h"
#include "command_parser.h"

#include "motor_task.h"
#include "balance.h"
#include "heading.h"
#include "bluetooth.h"
#include "battery_check.h"

#include <stdint.h>
#include <stdio.h>
#include <stdlib.h>
#include <string.h>
/* USER CODE END Includes */

ADC_HandleTypeDef hadc1;

I2C_HandleTypeDef hi2c1;

TIM_HandleTypeDef htim1;
TIM_HandleTypeDef htim2;
TIM_HandleTypeDef htim3;
TIM_HandleTypeDef htim4;
TIM_HandleTypeDef htim5;

UART_HandleTypeDef huart2;
UART_HandleTypeDef huart6;
DMA_HandleTypeDef hdma_usart2_rx;

/* USER CODE BEGIN PV */

// FSM Initialization
    HEADING heading = HEADING();
    BALANCE balance = BALANCE();
    MOTOR_TASK motor_task = MOTOR_TASK();
    BLUETOOTH bluetooth = BLUETOOTH();
    BATTERY_CHECK battery_check = BATTERY_CHECK();

// Declare BNO055
    BNO055_Sensors_t BNO055;	/*!BNO055 data structure definition which hold euler, quaternion, linearaccel, gyro etc. parameters*/

// Declare command parser class
    COMMAND_PARSER parser;

// Declare User button variable
    volatile bool USER = 0;

// Code for testing controller commands
    #define BUFFER_SIZE 64
    uint8_t rx_byte;
    uint8_t rx_buffer[BUFFER_SIZE];
    uint8_t buffer_index = 0;
    volatile uint8_t command_ready = 0;


// Code for initializing velocity setpoint for laptop bluetooth control
    int32_t AR = 0;
    int32_t V = 0;

/* USER CODE END PV */

void SystemClock_Config(void);
static void MX_GPIO_Init(void);
static void MX_DMA_Init(void);
static void MX_ADC1_Init(void);
static void MX_I2C1_Init(void);
static void MX_TIM1_Init(void);
static void MX_TIM3_Init(void);
static void MX_TIM4_Init(void);
static void MX_TIM5_Init(void);
static void MX_USART2_UART_Init(void);
static void MX_USART6_UART_Init(void);
static void MX_TIM2_Init(void);
/**
  * @brief  The application entry point.
  * @retval int
  */
int main(void)
{

  /* MCU Configuration--------------------------------------------------------*/

  /* Reset of all peripherals, Initializes the Flash interface and the Systick. */
  HAL_Init();

  /* Configure the system clock */
  SystemClock_Config();

  /* Initialize all configured peripherals */
  MX_GPIO_Init();
  MX_DMA_Init();
  MX_ADC1_Init();
  MX_I2C1_Init();
  MX_TIM1_Init();
  MX_TIM3_Init();
  MX_TIM4_Init();
  MX_TIM5_Init();
  MX_USART2_UART_Init();
  MX_USART6_UART_Init();
  MX_TIM2_Init();
  /* USER CODE BEGIN 2 */
  UART_DMA_IDLE_Init(&huart2);	// Start DMA IDLE Line detection.

  Sensor_Init();  	//Initialization of BNO055 sensor groups

  // Code for setting modified velocity
  AR = htim1.Init.Period;
  //  V = (AR * 20) / 100;	// 20% Velocity Modifier
  V = 5000;	// Velocity setpoint in encoder counts per second
  HAL_TIM_Base_Start(&htim2);	// Start timer 2 to allow use of time_utils

  /* USER CODE END 2 */

  /* Infinite loop */
  /* USER CODE BEGIN WHILE */
  while (1)
  {
      // The following block of code is meant for use while the robot is connected to a laptop/computer
	// and is being controlled using the arrow keys through use of robot_controller.py

//      if (command_ready) {
//          bluetooth.set_command(rx_buffer[0]);  // First char of command
//          command_ready = 0;
//      }
//      bluetooth.run();	// Run bluetooth task that generates motor commands based on laptop keyboard input
//      balance.run();		// Run balance task that balances the robot based on Euler Angle data from the IMU
//				  // In theory, the balance code should work with my lab partner's controller. However,
//				  // this remains untested

      // The following block of code is meant for use while the robot is being controlled by my lab
      // partner's smart knob controller

      parser.parse();	// Run command parsing script to generate motor commands based on smart knob input
      heading.run();	// Run heading control task to generate motor commands based on the robot's heading

      // The following block of code should always run, regardless of the controller input

      motor_task.run();		// Run motor control task to receive commands from controller tasks
				  // and apply PWM duty cycle accordingly
      battery_check.run();	// Run battery check task to turn on an LED when battery is too low
      HAL_Delay(1);		// Slight delay to prevent control loops from running too fast

    /* USER CODE END WHILE */

    /* USER CODE BEGIN 3 */
  }
  /* USER CODE END 3 */
}

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
/* USER CODE BEGIN 4 */

// User Button Interrupt
void HAL_GPIO_EXTI_Callback(uint16_t GPIO_Pin) {
    if (GPIO_Pin == GPIO_PIN_15) {  // PB15
        USER = 1;  // Set User Button flag
    }
}
/* USER CODE END 4 */
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


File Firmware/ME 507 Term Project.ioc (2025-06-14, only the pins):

Mcu.UserName=STM32F411CEUx
PA0-WKUP.Signal=S_TIM5_CH1
PA1.Signal=S_TIM5_CH2
PA11.Signal=USART6_TX
PA12.Signal=USART6_RX
PA13.Signal=SYS_JTMS-SWDIO
PA14.Signal=SYS_JTCK-SWCLK
PA2.Signal=USART2_TX
PA3.Signal=USART2_RX
PA5.Signal=S_TIM2_CH1_ETR
PA6.Signal=S_TIM3_CH1
PA7.Signal=S_TIM3_CH2
PA8.Signal=S_TIM1_CH1
PA9.Signal=S_TIM1_CH2
PB0.Signal=ADCx_IN8
PB12.Signal=GPIO_Output
PB15.Signal=GPXTI15
PB3.Signal=SYS_JTDO-SWO
PB6.Signal=S_TIM4_CH1
PB7.Signal=S_TIM4_CH2
PB8.Signal=I2C1_SCL
PB9.Signal=I2C1_SDA

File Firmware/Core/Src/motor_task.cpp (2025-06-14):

/*
 * motor_task.cpp
 *
 *  Created on: Jun 2, 2025
 *      Author: jacka
 */

#include "motor_task.h"

/**
 * @brief Constructor for the MOTOR_TASK class.
 * @details Initializes the FSM state and configures motor and encoder objects.
 */
MOTOR_TASK::MOTOR_TASK() : state(S0_INIT),
motor1{ .duty = 0, .htim = &htim1, .ch_A = TIM_CHANNEL_1, .ch_B = TIM_CHANNEL_2 },
motor2{ .duty = 0, .htim = &htim5, .ch_A = TIM_CHANNEL_1, .ch_B = TIM_CHANNEL_2 }
{

}

/**
 * @brief Checks whether the motor task should be running.
 * @return True if any setpoints or efforts from control modules are non-zero.
 */
bool MOTOR_TASK::should_run() {
    return (parser.get_M1_set() != 0) ||
           (parser.get_M2_set() != 0) ||
           (bluetooth.get_M1_set() != 0) ||
           (bluetooth.get_M2_set() != 0) ||
           (heading.get_M1_eff() != 0.0f) ||
           (heading.get_M2_eff() != 0.0f) ||
           (balance.get_M1_eff() != 0.0f) ||
           (balance.get_M2_eff() != 0.0f);
}

/**
 * @brief Executes one iteration of the MOTOR_TASK FSM.
 * @details Manages motor state transitions, runs PID control using encoder feedback,
 *          and integrates control efforts from balance and heading modules.
 */
void MOTOR_TASK::run(void)
{
    switch (state)
    {
        case S0_INIT:
            // Initialize motors and encoders
            motor_enable(&motor1);
            motor_enable(&motor2);
            M1_set = 0;
            M2_set = 0;
            motor_set_duty(&motor1, M1_set);
            motor_set_duty(&motor2, M2_set);

            encoder_init(&encoder1, &htim3);
            encoder_init(&encoder2, &htim4);
            encoder_reset(&encoder1);
            encoder_reset(&encoder2);

            // Set PID gains
            Kp1 = 1.2;
            Ki1 = 6;
            Kd1 = 0.0f;
            Kp2 = 1.2;
            Ki2 = 6;
            Kd2 = 0.0f;

            state = S1_IDLE;
            break;

        case S1_IDLE:
            // Motors idle and waiting for activity
            motor_set_duty(&motor1, 0);
            motor_set_duty(&motor2, 0);

            encoder_update(&encoder1);
            encoder_update(&encoder2);
            last_time = micros();

            // Reset PID state
            error1 = error2 = prev_error1 = prev_error2 = 0;
            error_diff1 = error_diff2 = 0;
            error_sum1 = error_sum2 = 0;

            if (should_run()) {
                state = S2_RUN;
            }
            break;

        case S2_RUN:
            // Get setpoints: prefer parser over Bluetooth
            M1_set = (parser.get_M1_set() != 0) ? parser.get_M1_set() : bluetooth.get_M1_set();
            M2_set = (parser.get_M2_set() != 0) ? parser.get_M2_set() : bluetooth.get_M2_set();

            encoder_update(&encoder1);
            encoder_update(&encoder2);

            now = micros();
            dt = now - last_time;
            if (dt == 0) dt = 1;
            last_time = now;

            // Calculate PID error terms
            error1 = M1_set - encoder_getspeed(&encoder1);
            error2 = M2_set - encoder_getspeed(&encoder2);

            error_sum1 += error1 * dt;
            error_sum2 += error2 * dt;

            // Anti-windup clamp
            if (error_sum1 > 1500000000) error_sum1 = 1500000000;
            if (error_sum1 < -1500000000) error_sum1 = -1500000000;
            if (error_sum2 > 1500000000) error_sum2 = 1500000000;
            if (error_sum2 < -1500000000) error_sum2 = -1500000000;

            error_diff1 = error1 - prev_error1;
            error_diff2 = error2 - prev_error2;
            prev_error1 = error1;
            prev_error2 = error2;

            // PID control output
            M1_eff = (Kp1 * (float)error1)
                   + (Ki1 * (float)error_sum1 / 1000000.0f)
                   + (Kd1 * (float)error_diff1 * 1000000.0f / (float)dt);

            M2_eff = (Kp2 * (float)error2)
                   + (Ki2 * (float)error_sum2 / 1000000.0f)
                   + (Kd2 * (float)error_diff2 * 1000000.0f / (float)dt);

            // Add control efforts from heading and balance FSMs
            M1_eff += heading.get_M1_eff();
            M2_eff += heading.get_M2_eff();
            M1_eff += balance.get_M1_eff();
            M2_eff += balance.get_M2_eff();

            // Clamp output effort to safe range
            M1_eff = std::max(-4799.0f, std::min(M1_eff, (float)4799.0f));
            M2_eff = std::max(-4799.0f, std::min(M2_eff, (float)4799.0f));

            motor_set_duty(&motor1, (int32_t)M1_eff);
            motor_set_duty(&motor2, (int32_t)M2_eff);

            if (!should_run()) {
                state = S1_IDLE;
            }
            break;

        default:
            motor_disable(&motor1);
            motor_disable(&motor2);
    }
}

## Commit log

2025-06-14 Initial commit: STM32 project setup and Doxygen documentation
2025-06-14 Fix folder case: rename Docs to docs for GitHub Pages
2025-06-14 Addded Firmware README with STM32 Project Details
2025-06-14 Created README.md for Firmware folder with information for the STM32 Project
2025-06-16 Added robot BOM, hardware README; update firmware README; removed unused fastener
    [M3_M_TO_F_10MM_STANDOFF.STEP, Robot BOM.csv]
2025-06-16 Re-worded Hardware README and changed some file/folder names for clarity
    [37d-gearmotor-19-30-encoder.step, Robot BOM.csv, pololu-universal-aluminum-mounting-hub-for-6mm-shaft-m3-holes.step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]

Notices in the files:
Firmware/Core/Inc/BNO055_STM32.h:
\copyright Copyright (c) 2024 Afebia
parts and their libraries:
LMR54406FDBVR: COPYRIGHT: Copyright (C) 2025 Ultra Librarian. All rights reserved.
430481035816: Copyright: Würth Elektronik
